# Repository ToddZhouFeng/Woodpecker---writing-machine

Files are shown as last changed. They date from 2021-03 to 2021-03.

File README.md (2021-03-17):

# Woodpecker

> 一个简单、低成本、可DIY的写字机器人
>
> A simple, low price, DIYable writing machine

## 项目介绍

### 为什么我要做这个？

目前大多数写字机器人的成本都很高，淘宝上的最低也要500，而开源的也要2~3百。在我看来，写字只是一件很简单的事，根本不需要这么多钱。因此，我希望能设计出一款低于百元的写字机器人。

我大致看了一下网上的开源方案，比较有代表性的如 github 上的 [peng-zhihui/X-Bot](https://github.com/peng-zhihui/X-Bot) 和 arduino社区的 [写字机器人](https://www.arduino.cn/thread-93897-1-1.html)，使用的基本是 core-XY（XY联动）方案，这种方案的介绍可以看 [peng-zhihui/X-Bot](https://github.com/peng-zhihui/X-Bot)，简单来说就是十字交叉的「同步带+导轨」+两个伺服电机

这种方案基本上可以无缝用于工业了好吧╮(╯-╰)╭，不贵才怪呢！个人使用的无需这么复杂。于是就有了这个项目。下面来说说我的想法。

补充资料：

* [3D打印机设计：关于 CoreXY 与 H-bot 之间的选择](https://blog.libcore.org/?p=291)
* [H-BOT机械手模型](http://bbs.inovance.com/course/67/207)

### 我的想法

作为非机械系学生，我希望结构越简单越好。首先，电机直接控制笔在两个方向上的运动。两者要如何连接呢？自然而然，我想到了线。用线的话，就不能在水平面，而是要在垂直面上控制笔——纸固定在墙上，上面挂两个电机，电机用线吊着笔。显然，这种方案在数学上是可行的，给定两根线长，可以求出笔在纸上的位置。

那么，如何控制笔的起落呢？这个可以借鉴以前的开源方案，用一个小舵机来控制笔的旋转，从而控制笔与纸的接触。

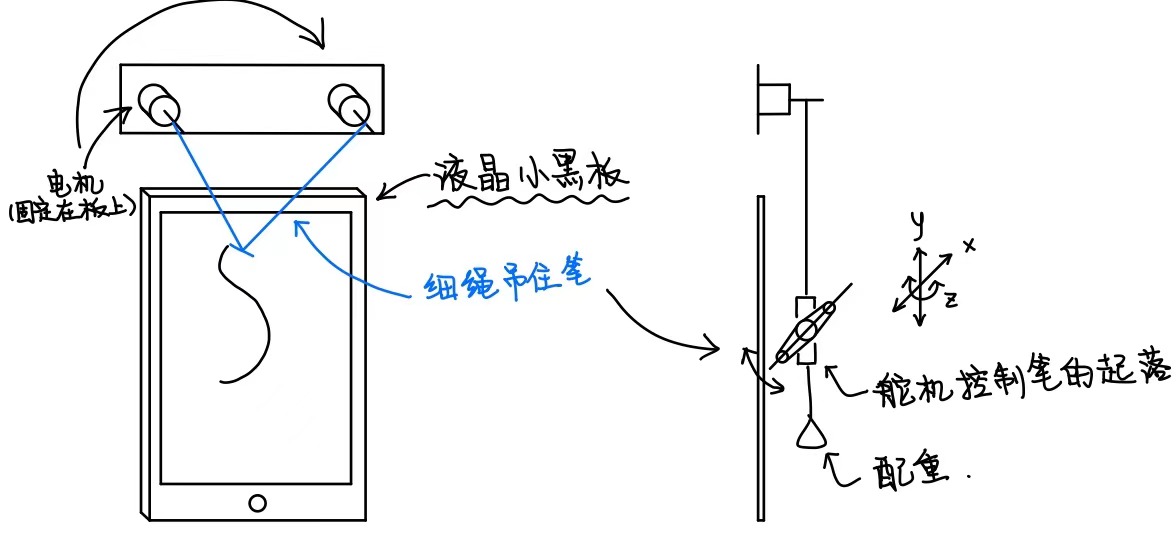
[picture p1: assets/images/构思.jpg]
构思


至此，大概雏形就已经出来了。当然，我不是第一个提出的这种方案的人，网上已经有 DIY 教程：[instructables - Polargraph Drawing Machine](https://www.instructables.com/Polargraph-Drawing-Machine/)，这家伙甚至写好了代码！Bravo！

但这只是节省了导轨的成本，并没有节省伺服电机的成本。于是我想，笔这玩意又没多重，应该用步进电机就行了吧，看网上资料说步进电机没有累积误差，那我直接计算转的圈数就能获取当前的绳长。如果有失步，或许可以通过中途再校正来消除。

OK，想法有了，开干！

## 设计过程

### 硬件

需要的硬件有：

* 步进电机28BYJ-48 + 驱动板 2 套 共￥9.6
* 舵机SG90 1 个 ￥3.9
* 细长线 2 条 ￥0（找妈要）
* 杜邦线母对母、公对母 若干条 ￥1
* 5V电源 1 个 ￥2
* 热熔胶 ￥9.3
* 可选：液晶小黑板（省得老是换纸）米家的贵一点（￥48.9），淘宝上有 ￥9.9 包邮的

总共：￥25.8（不考虑液晶小黑板）

另外还需要控制设备。如果使用上位机与下位机分离的方式，电脑作为上位机，下位机可以是 arduino、stm32、esp8266；如果上位机与下位机一体，可以使用树莓派 zero. 控制设备大概要花费 ￥70

因为我有树莓派，所以我直接在树莓派上控制。

#### 3D 打印

需要 3D 打印的部分有：步进电机固定座、轴套、舵机固定座、笔托。这里问题比较大的是舵机固定座和笔托。因为在初次实验中，我发现写字时笔会歪，导致笔不可能垂直于纸。要解决这个问题，我设想了几个方案：

* 如果是液晶小黑板，则将直杆形的笔换成圆盘性的笔，这样就能解决左右歪的问题，至于上下歪，可以通过增加配重来解决。
* 如果是一般的笔，可以直接在舵机固定座两边加上泡沫支撑
* 双绳方案：增加多一条绳（会增加安装难度

### 软件

第一个问题是，如何将 x-y 坐标的图像，转换为双极坐标？

第二个问题是，给定一条曲线，如何控制步进电机？如果要考虑下笔的轻重，那如何控制舵机？

第三个问题是，如何将图像/文字转化成线？

第四个问题是，怎么规划路径？或者说，怎么决定笔画的顺序？

#### 问题一

双极坐标（Bipolar Coordinates）的定义如下：A,B 是两固定点，距离为 w，平面上任意一对点都可以用到 A,B 的距离 a,b 来表示。详细介绍请去看：[百度百科](https://baike.baidu.com/item/%E5%8F%8C%E6%9E%81%E5%9D%90%E6%A0%87%E7%B3%BB/22803822) 和 [维基百科](https://zh.wikipedia.org/zh-hans/%E9%9B%99%E6%A5%B5%E5%9D%90%E6%A8%99%E7%B3%BB)

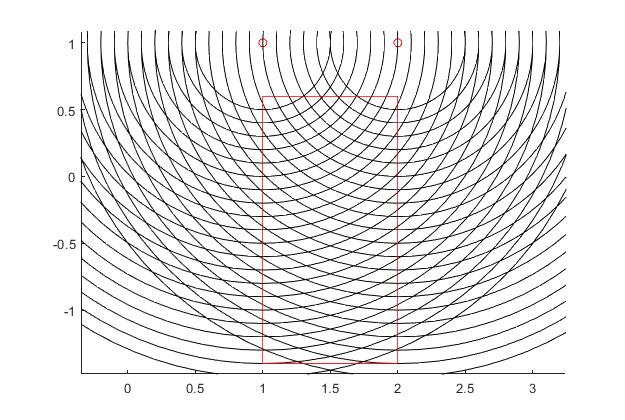
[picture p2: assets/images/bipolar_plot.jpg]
双极坐标


坐标系变换这个应该是在高等数学中学的。我们要实现的就是如下变换：

<center>(x,y)\leftrightarrow(a,b)</center>

一般来说，(x,y) 原点在图像的左下角，但对于悬挂式的写字机器人，图像是从左上角开始画的，所以我们规定左上角是为原点。这么一来，就有：

<center>\begin{cases} a=\sqrt{x^2+y^2}\\ b=\sqrt{(w-x)^2+y^2} \end{cases}</center><br>

<center>\begin{cases} x=\frac{a^2+w^2-b^2}{2w}\\ y=\frac{1}{w}\sqrt{(aw)^2-\left(\frac{w^2+a^2-b^2}{2}\right)^2} \end{cases}</center>

图像转换成双极坐标后，我们就可以像在直角坐标下那样思考。后面默认都是双极坐标。

#### 问题二

步进电机的原理很简单，就是通过磁场的旋转，来带动转子转动。磁场又是通过脉冲控制的，那样只要知道初始位置和脉冲数量，就知道笔的位置。

[步进电机28BYJ-48拆机图、原理和51/stm32测试程序](https://blog.csdn.net/wangguchao/article/details/78902212)

#### 问题三

见 ImagePreprocess

这里我参考了 [Samir55/Image2Lines](https://github.com/Samir55/Image2Lines)、[arthurflor23/text-segmentation](https://github.com/arthurflor23/text-segmentation)、[A Statistical approach to line segmentation in handwritten documents](https://cedar.buffalo.edu/~srihari/papers/SPIE-2007-lineSeg.pdf)

#### 问题四

见 PathDecide

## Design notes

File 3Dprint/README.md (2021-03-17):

# 3D打印模型设计

## 步进电机固定板

28BYJ-48 的尺寸图见：[28BYJ-48 Stepper Motor - RoboCraft](http://robocraft.ru/files/datasheet/28BYJ-48.pdf)

## 步进电机轴套

转轴是一个被削了两刀的圆柱，外圆 4.96mm（取 5mm） 两截面 2.92mm（取 3mm）轴长 6mm，

axis_shell.ptr

## 舵机固定板

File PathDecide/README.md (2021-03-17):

# 路径决策

本模块要解决如何通过位图来驱动电机，这是本项目的核心模块。我们规定以下对象和接口：

* `bitmap` 位图（二维矩阵，值为0或1，1表示要下笔的地方），大小为 a_max × b_map
* `index2length(index_a, index_b)` 由位图像素的索引计算出长度
* `drop()` 和 `lift()`
* `motor_a` 电机a
  * `motor_a.move(thread_length)` 移动到对应长度
* `motor_b` 电机b
  * `motor_b.move(thread_length)` 移动到对应长度

## 扫描法

顾名思义。优点是简单，缺点是慢。

```python
for k in range(a_max):
    for l in range(b_max):
        if bitmap[l,k]==1:
            drop()
        else:
            lift()
        thread_length_a, thread_length_b = index2length(k,l)
        motor_a.move(thread_length_a)
        motor_b.move(thread_length_b)
```

为了提高效率，我们可以考虑采用跳跃扫描法（实际是缩减分辨率）。如下：

```python
for k in range(0,a_max,2):
    for l in range(0,b_max,2):
        if bitmap[l,k]==1 or bitmap[l+1,k]==1 or \
            bitmap[l,k+1]==1 or bitmap[l+1,k+1]==1:
            drop()
        else:
            lift()
        thread_length_a, thread_length_b = index2length(k,l)
        motor_a.move(thread_length_a)
        motor_b.move(thread_length_b)
```

## 深度搜索法

简单来说就是先扫描，当找到第一个下笔点后，从下笔点开始不断向外搜索，并移动。当找不到时，抬笔，再次向外搜索，然后找到下笔点后，再重复前面的过程。如下：

```python
while True:
    index_next=search(image, index_now)
    if index_next == None:
        break
    if not is_next_to(index_next, index_now):
        if is_drop():
            lift()
        else:
            drop()
    thread_length_a, thread_length_b = index2length(index_next[0],index_next[1])
    motor_a.move(thread_length_a)
    motor_b.move(thread_length_b)
    image[index_now[0], index_now[1]] = 0
```

但这只能达到局部最优，而不能达到全局最优。举个例子，假如说要写一个 T 字，显然，先写一横，再写一竖是最快的，但有可能会先写一个“7”，再补回横的后面，这样的效率就不高。

那这样，我想可以先搜索出所有路径（深度优先或广度优先都行），然后从路径中选择一条最短的路径。这种策略就可以解决上面的问题。

但上面的策略并不完美，比如说要写一个 R 字，从左下开始，如果是选择最短的路径，则会写一个“∧”，然后再写上面的圈。但最快的方式显然是先写一竖 |，再写半圈 ﹚，最后写右下一捺，这样可以一笔写完。（不知道说不说得清……）

于是咱的策略又要改变，我们需要知道最短与最长的路径。如果最长的路径可以覆盖当前的连通区域，那么就选择最长的路径，否则，选择最短的路径。

但这种方法的复杂度很高。为了减少复杂度，我认为在搜索路径时，可以只取某几个方向。比如上一步是向上搜索，那么下一步就只能搜索上面的三个像素。（也就是把一段弯折的线看作不同线段）

算了，太复杂了😫别搜索所有路径了，直接按第一段来吧。

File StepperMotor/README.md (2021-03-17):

# 电机驱动

要驱动电机使线到达指定长度，就必须要知道初始长度以及电机步数。初始长度可以通过手动调整到指定位置，或者手动输入初始长度。电机步数则用一个无符号整型记录即可。另外，最好能知道当前转子的状态，这样的话步就能以拍为单位精确调整。

我们用 `steps_now` 来表示电机当前的步数，`step_length` 表示步长（以拍为单位），一拍的转动长度 `stride_length` 约等于 0.0046mm，则线长 `thread_length=steps_now*step_length*stride_length`。

步进电机我们采用 8 拍的驱动方式，即：

| 转子状态 | 0 | 1 | 2 | 3 | 4 | 5 | 6 | 7 |
| --- | --- | --- | --- | --- | --- | --- | --- | --- |
| P1-红 | VCC | VCC | VCC | VCC | VCC | VCC | VCC | VCC |
| P2-橙 | GND | GND | | | | | | GND |
| P3-黄 | | GND | GND | GND | | | | |
| P4-粉 | | | | GND | GND | GND | | |
| P5-蓝 | | | | | GND | GND | GND | |

我们定义当前的转子状态 `motor_state_a` 与步数 `steps_now_a` 、步长 `step_length` 的关系如下：

```python
motor_state = (steps_now_a * step_length) % 8
```

初始化时，用户要调整电机，使得笔恰好对齐某个位置，这个位置的线长是固定的（在组装时设置好），假设是 `init_thread_length`，则初始时的步数为：

```python
steps_now = int(init_thread_length / (step_length * stride_length))
```

但如果我们想要精确到拍的话，上面的初始过程就不够好。所以我们规定，在用户调整电机时，转子始终停在 0 状态，并且初始步数要被 8 整除：

```python
steps_now -= steps_now % 8 
```

之后在写字的过程中，如果要去到 `thread_length` 位置，需要移动的步数为：

```python
int(thread_length/step_length/stride_length)-steps_now
```

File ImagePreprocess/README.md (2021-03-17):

# 图像预处理 ImagePreprocess

对待显示的图像/文字进行预处理，得到适合写字机器人的双极坐标下的二值位图（点阵图）。除了进行坐标变换外，还需要对图像进行一系列处理，以获得更好的显示效果。

处理工序：（名字是我随便起的）

* 像素二值化
* 图像素描化
* 线条归一化
* 上采样/下采样
* 分辨率对齐（坐标变换）

注：工序的顺序有待后续进一步实验。

## 分辨率

对输入的源图像，及输出的位图的分辨率的讨论。

### 液晶板的分辨率

液晶小黑板上的笔记会随写字的力度变化，大概在 0.4~1.5mm 之间。一般的纸和笔则是在0.4~0.7mm 之间。而

* 10英寸米家小黑板的可写面积大概是：150×200mm，也就是说，分辨率最高为 375×500，最低为 100×133
* 淘宝上9.9包邮的8.5英寸小黑板的可写面积为 120×174mm，对应的最高分辨率为 300×435，最低为 80×116

实验时，我们使用8.5英寸的小黑板，并取笔记粗细为 0.6（方便计算），则分辨率为 200×290. 要清晰显示一个汉字，至少要 16×16（不考虑[丁卯点阵体](https://3type.cn/fonts/dinkie_bitmap/index.html)），这么一来，我们一共能显示 12×16=192字，用作备忘录应该可以了（用作情书得增加分辨率才行）。

### 步进电机分辨率

但除了液晶小黑板的分辨率外，我们还要考虑笔的最小移动距离，即步进电机的最小转动距离。

28BYJ-48 是四相八拍减速型步进电机，转子转动一圈需要 64 拍，而减速比为 1:64，从而转轴转一圈需要 4096 拍。（参考自 [太极创客 - 28BYJ-48单极性步进电机](http://www.taichi-maker.com/homepage/reference-index/motor-reference-index/28byj-48-stepper-motor-intro/)）

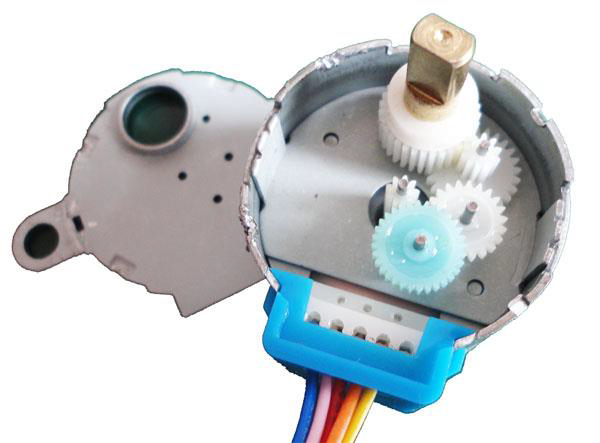
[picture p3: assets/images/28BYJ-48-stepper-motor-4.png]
28BYJ-48步进电机内部拆解图


由于转轴不是圆的，所以需要在外部套上轴套（3D打印），设轴套直径为 5mm，考虑上线缠绕会增加 1mm 左右，也就是总共 6mm。那么，最小转动距离为 π×6÷4096 ≈ 0.0046mm

只有当线垂直时，笔的最小移动距离才等于最小转动距离，当不垂直时，情况会比较复杂，有可能大于也有可能小于最小转动距离（见下图红框的下部，纵向小于，横向大于）

<center>双极坐标下的网格点</center>

由于最小移动距离并不是唯一的，为了避免误解，我们使用“格点距离”来表示笔的移动距离。格点距离 $d$ 可以用如下公式计算：设 P 点的双极坐标为 $(a_p,b_p)$，Q 点的双极坐标为 $(a_q,b_q)$，极点间距为 $w$，则根据余弦公式：

$$
\sec \left( \arccos\left(\frac{a_p^2+w^2-b_p^2}{2a_pw}\right)-\arccos \left( \frac{a_q^2+w^2-b_q^2}{2 a_q w} \right) \right)=\frac{a_p^2+a_q^2-d^2}{2a_p a_q}
$$

我们可以利用反三角函数公式化简：

$$
记\, x=\frac{a_p^2+w^2-b_p^2}{2a_pw}, y=\frac{a_q^2+w^2-b_q^2}{2 a_q w}\\
则\, xy+\sqrt{(1-x^2)(1-y^2)}=\frac{a_p^2+a_q^2-d^2}{2a_p a_q}
$$

继续化简：

$$
\begin{aligned}
    d^2=&a_p^2+a_q^2 - 2 a_pa_q\left(xy+\sqrt{(1-x^2)(1-y^2)}\right)\\
    =&a_p^2+a_q^2 - \frac{(a_p^2+w^2-b_p^2)(a_q^2+w^2-b_q^2)}{2 w^2}\\
    &\frac{1}{2w}\sqrt{(2a_p w)^2 - (a_p^2+w^2-b_p^2)^2 }\sqrt{(2 a_q w)^2 - (a_q^2+w^2-b_q^2)^2}
\end{aligned}
$$

尴尬了，matlab 没装 symbolic math toolbox 求不了导，随便取几组数据吧。取 $w=100$，$\Delta=0.0046$：

|原位置(线长)|移动后|距离|
|-----|-----|---|
|(57.73,57.74)|(+Δ,-Δ)|0.0053|
|(57.73,57.74)|(+Δ,+Δ)|0.0092|
|(186.81,186.82)|(+Δ,-Δ)|0.0172|
|(186.81,186.82)|(+Δ,+Δ)|0.0048|

实际的最小转动距离并不会取这么小，感觉可以乘个 25，故取 $\Delta=0.115$

|原位置(线长)|移动后|距离|
|-----|-----|---|
|(57.73,57.74)|(+Δ,-Δ)|0.1328|
|(57.73,57.74)|(+Δ,+Δ)|0.2293|
|(186.81,186.82)|(+Δ,-Δ)|0.4297|
|(186.81,186.82)|(+Δ,+Δ)|0.1194|

观察上面几组数据，可以得出以下结论：

1. 当笔靠近上面时，横向格点距离与最小转动距离差不多，纵向则是 2 倍关系
2. 当笔靠近下面时，纵向格点距离与最小转动距离差不多，横向则是 4 倍关系
3. 在可写面积内，基本上不会出现格点距离小于最小转动距离的情况，因此可以认为最小格点距离就是最小转动距离。

### 输出位图的分辨率

尽管实际显示的分辨率仅有 200×290（液晶小黑板的分辨率），但输出位图的分辨率应该比这个大。我们可以用下图来说明原因。

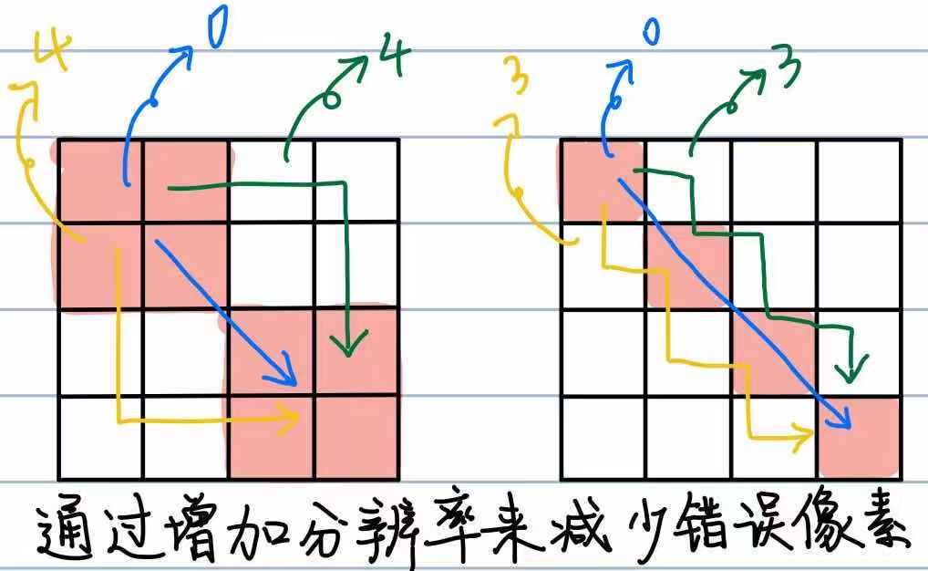
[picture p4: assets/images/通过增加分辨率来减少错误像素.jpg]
通过增加分辨率来减少错误像素


图片中的涂红部分为要落笔的像素点，如果要从一个像素移到另一个像素，可以使用多种驱动电机的方式，最简单的有三种：①先左电机后右电机、②先右电机后左电机、③同时驱动。

同步驱动对控制的要求比较高，并且完全同步是不可能的。而另外两种在移动的过程中都会误涂到空白像素，上图中标出的数字就是误涂面积。一种减少误涂面积的方法就是增加分辨率，减小每次移动的距离。

当然，图像的分辨率也不是越大越好，太大的话，后面路径规划的计算时间会很长，并且画图的时间也很长。另外，分辨率的上限也受到最大格点距离（最小转动距离）的影响。~~如果取最小转动距离为 0.115（25拍）：宽 120/0.115=1043，高 174/0.115=1513（大概是 1080P）~~。

输出位图具体的分辨率将在“分辨率对齐”一节再深入讨论。

## 分辨率对齐（坐标变换）

分辨率对齐指的是数字图像映射到实际的纸上，此处的“数字图像”有两个：输入的源图像以及输出的位图。理想的情况是源图像和位图均重合于实际的纸上，不过实际中必然存在一定偏差，我们要尽可能减小偏差。

首先我们需要确定两电机之间、纸于电机之间的距离。

两电机无论是直接粘在墙上，还是先粘在框架上，它们之间的距离大概能精确至 1mm。假设这个距离是 $w$. 同时，我们假设两电机在一条水平线上（误差 $\pm 1^\circ$），这样，我们就能在空间中建立双极坐标系和直角坐标系（以坐电机为原点）。

我们又假设纸是正的（误差 $\pm 1^\circ$），左上、右上、右下、左下角用 $P_1,P_2,P_3,P_4$ 表示。设纸的左上角 $P_1$ 点的直角坐标为 $(x_1,y_1)$，纸的宽度为 $w_p$，高度为 $h_p$（同样精确到 1mm）。

设源图像的分辨率为 $w_i \times h_i$，并且图像尽可能铺满纸。那么，纸上的每个点 $(x,y) \in \mathbb{R}^2$ 与像素 $(m,n) \in \mathbb{N}^2$ 满足如下对应关系：

$$
w_g = \min\{ \frac{w_p}{w_i}, \frac{h_p}{h_i} \}\\
\lceil\frac{x-x_1}{w_g}\rceil=m\\
\lceil\frac{y-y_1}{w_g}\rceil=n \tag{1}
$$

这里的像素从左上角开始数起，恰好与 opencv 中一致。$w_g$ 是像素格（grid）的边长。上述就是输入的源图像映射到纸上的过程

然后我们再将位图映射到纸上。不过我们需要先确定位图的分辨率。假设最小转动距离为 $w_r$，线的长度的取值范围为：

$$
a\in[\sqrt{x_1^2+y_1^2},\sqrt{x_3^2+y_3^2}]\\
b\in[\sqrt{(w-x_2)^2+y_2^2},\sqrt{(w-x_4)^2+y_4^2}] \tag{2}
$$

则分辨率为：$\lceil\dfrac{a_\max}{w_r}\rceil\times\lceil\dfrac{b_\max}{w_r}\rceil$，其中每个像素点 $(k,l) \in \mathbb{N}^2$ 与空间中的点 $(x,y) \in \mathbb{R}^2$ 满足如下对应关系：

$$
\frac{(k w_r)^2+w^2-(lw_r)^2}{2w}=x\\ 
\frac{1}{w}\sqrt{(k w_rw)^2-\left(\frac{w^2+(k w_r)^2-(lw_r)^2}{2}\right)^2}=y \tag{3}
$$

把公式 $(3)$ 代入公式 $(1)$ 就能得到不同坐标下的像素对应关系：

$$
m=\lceil\frac{(k w_r)^2+w^2-(lw_r)^2}{2ww_g}-\frac{x_1}{w_g}\rceil\\
n=\lceil \frac{1}{w w_g}\sqrt{(k w_rw)^2-\left(\frac{w^2+(k w_r)^2-(lw_r)^2}{2}\right)^2}-\frac{y_1}{w_g}\rceil
$$

python 程序见 cartesian2bipolar_v1.py，输入 (2000, 1500, 3) 的图片，最小转动距离取 0.0046mm，输出 (2333, 2333, 3) 的图片。经过处理后的图像为（左：输入；右：输出）：

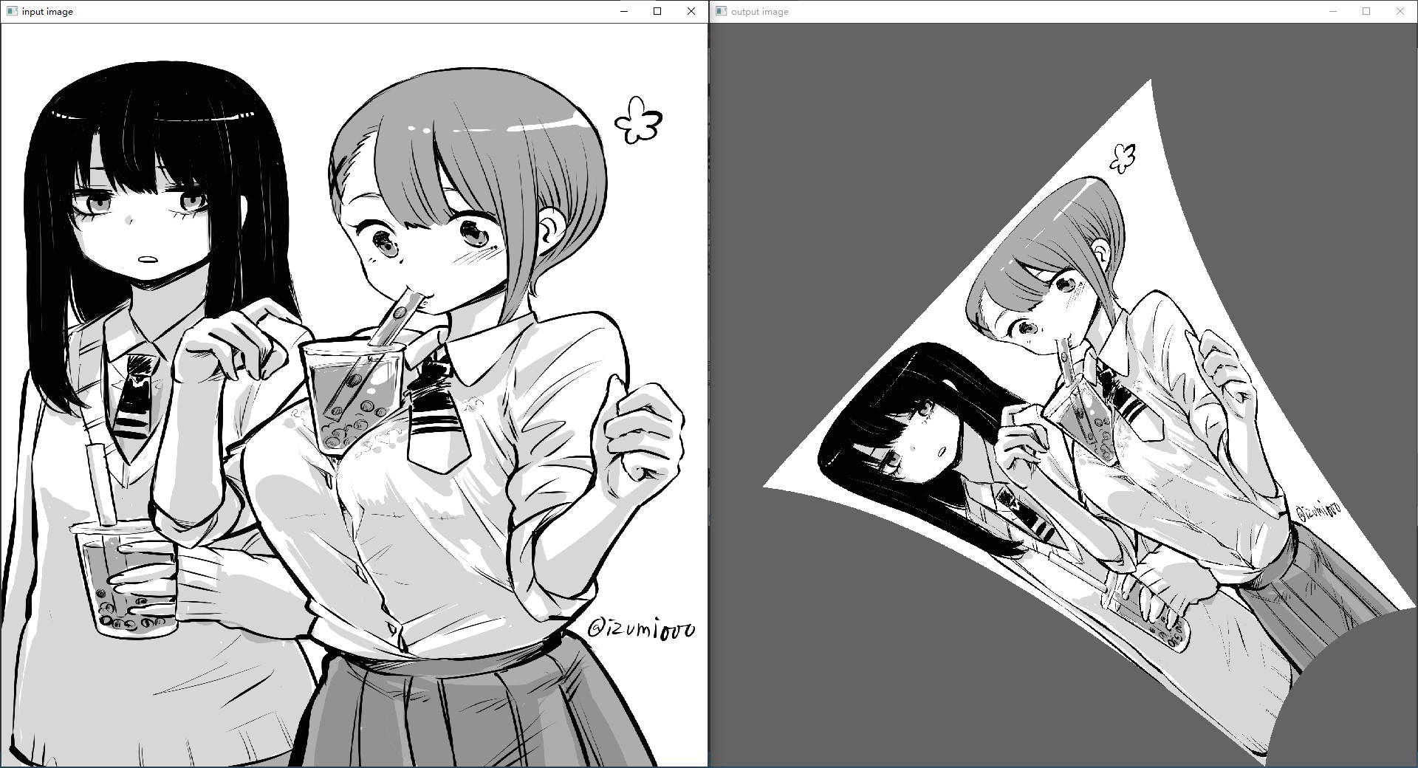
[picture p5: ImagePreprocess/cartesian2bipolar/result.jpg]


为了对比明显，我将图像外部用灰色来填充（实际中应该为纯白色）。注意到位图右下角好像被“挤压”了，说明这部分的图像清晰度有损失。（这也是这种写字机器人的缺点，图像的清晰度不均匀）

为了减小这部分损失，减小清晰度不均匀，我提出以下几种方案：

### 纸下移方案

尝试修改纸与电机的距离，从上面的 10mm，改为 100mm，得到下图：

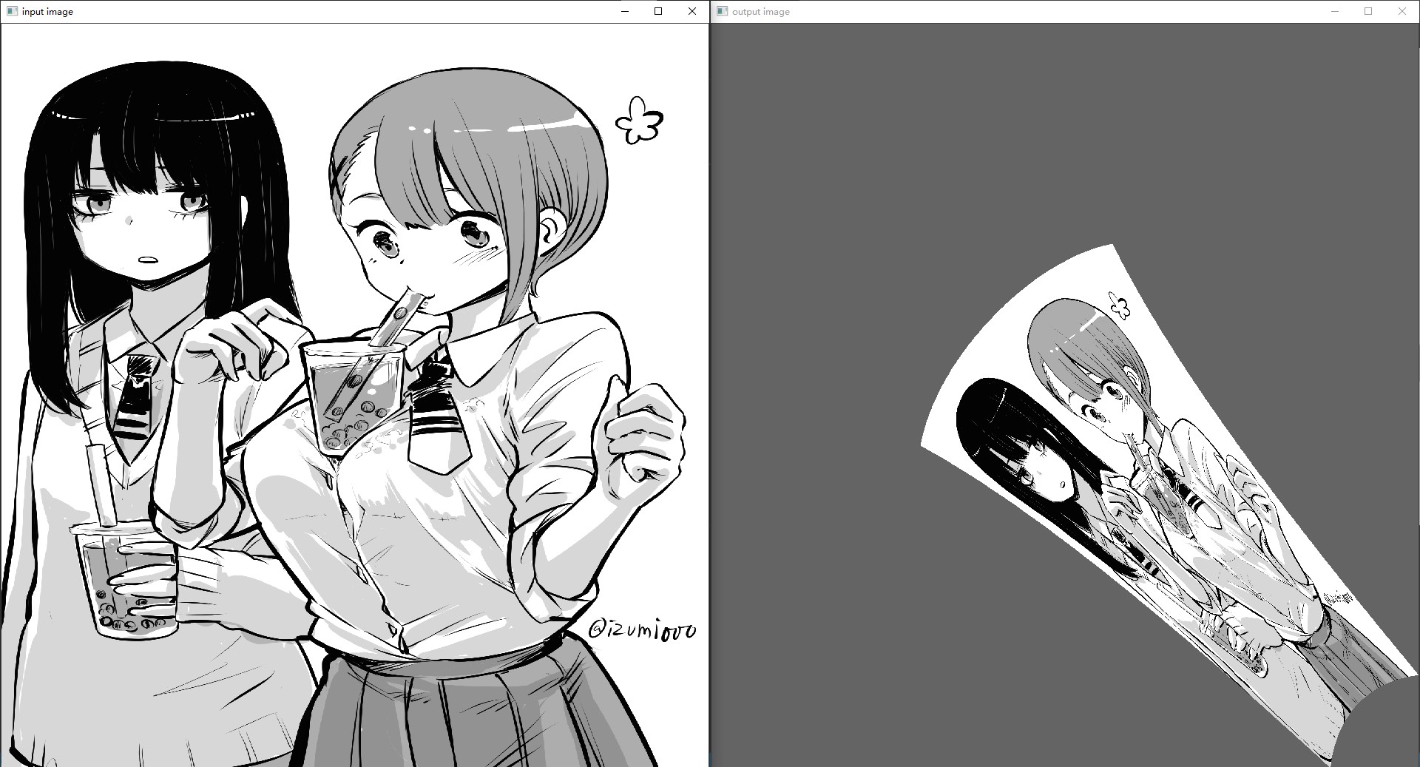
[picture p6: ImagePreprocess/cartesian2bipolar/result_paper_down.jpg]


注意到顶部和底部的分辨率差距减小了。这种方案的优点是：简单无脑。缺点嘛，就是使得写字机器人的占地变大了。

### 动态转动距离方案

引入“动态转动距离”方案。根据在“步进电机分辨率”一节的实验结论，当 $y$ 较小时（顶部），横向格点距离较大，当 $y$ 较大时（底部），横向格点距离较小。因此我们只需要改变一下位图像素索引与绳长的映射关系。原本的映射关系为：$(k,l)\rightarrow (kw_r,lw_r)$，现在假设映射关系为：$(k,l)\rightarrow (kw_r(y),lw_r(y))$，需要求解函数：$w_r(y)$

这个函数还挺复杂的……为了简单起见，我们规定转动距离取 $[w_{r\min},w_{r\max}]$ 中的整数值，即：

$$
w_r(y_\min)= w_{r\max}\\
w_r(y_\max)= w_{r\min}
$$

同时，观察位图左下的灰白交界线，感觉 $w_r(y)$ 应该是一个 $\ln$ 或 $\sqrt{\quad}$ 函数，假如是 $\ln$ 的话：

$$
w_r(y)= \lceil w_{r\min}+\frac{w_{r\max}-w_{r\min}}{\ln (y_\max-y_\min+1)}\ln (y_\max-y+1) \rceil
$$

假如是 $\sqrt{\quad}$ 的话：

$$
w_r(y)= \lceil w_{r\min}+\frac{w_{r\max}-w_{r\min}}{\sqrt{y_\max-y_\min}}\sqrt {y_\max-y}\rceil
$$

但是要求解 $y$，就必须要知道绳长……因此这种方案被我pass了

### 椭圆坐标方案

> 这个方案有点炫技的意味。

观察格点，我发现底部的曲率较大，这可能是造成底部格点距离较大的原因。因此我想能不能利用椭圆两端曲率较大的特点，减小底部的格点距离。

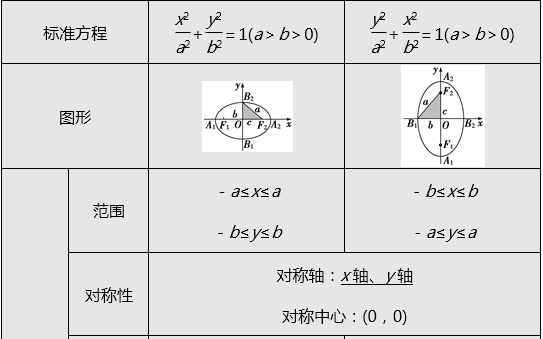
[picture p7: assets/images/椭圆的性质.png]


为此，我们需要对双极坐标进行改造。原本双极坐标的两个坐标变量 $(a,b)=(kw_r,lw_r)$ 表示的是到两个极点的距离，现在要变成椭圆坐标，每个极点需要改成两个焦点，同时，$(a,b)$ 表示为一对焦点间的距离。如果我们定义两个椭圆的表达式为：

$$
\frac{y^2}{a_A^2}+\frac{x^2}{b_A^2}=1\\
\frac{y^2}{a_B^2}+\frac{(x-w)^2}{b_B^2}=1\\
A 指左边的椭圆，B 指右边的椭圆
$$

$a_A,a_B$ 与 $b_A,b_B$ 保持某个比例，定义为 $\frac{a_A}{b_A}=\frac{a_B}{b_B}=\sec \beta$. 另外，$a_A=a$，$a_B=b$，即长轴的一半，这样的话，当 $\sec \beta=1$ 时，这种方案就能退化为之前的方案。

如果 $\sqrt{a_A^2-b_A^2} + \sqrt{a_B^2-b_B^2} \geq w$，则两个椭圆存在交点，交点求解如下：

$$
y^2+\frac{a_A^2 x^2}{b_A^2}=a_A^2\\
y^2+\frac{a_B^2(x-w)^2}{b_B^2}=a_B^2
$$

两式相减，有：

$$
[x^2-(x-w)^2]\cdot \sec^2 \beta = a_A^2-a_B^2
$$

整理后有：

$$
x=\frac{a_A^2-a_B^2}{2w\sec^2 \beta}+\frac{w}{2}
$$

代入回原式有：

$$
y=\sqrt{a_A^2-x^2 \sec^2 \beta}\\
（只取正值）
$$

实际的绳长为：

$$
\begin{cases} 
a'=\sqrt{x^2+y^2}\\ 
b'=\sqrt{(w-x)^2+y^2} 
\end{cases}
$$

另外我们还要计算位图的分辨率。纸的四个角还是用 $P_1,P_2,P_3,P_4$（左上、右上、右下、左下）表示，对应坐标为 $(x_1,y_1)$……，则 $a,b$ 的取值范围为：

$$
a\in \left[\sec \beta \sqrt{\frac{y_1^2}{\sec^2 \beta}+x_1^2}, \sec \beta \sqrt{\frac{y_1^3}{\sec^2 \beta}+x_1^3} \right]\\
b\in \left[\sec \beta \sqrt{\frac{y_2^2}{\sec^2 \beta}+x_2^2}, \sec \beta \sqrt{\frac{y_4^3}{\sec^2 \beta}+x_4^3} \right]
$$

下面是这种方案的验证结果，$\sec \beta$ 取 $1.2$（程序见 cartesian2bipolar_v2.py）

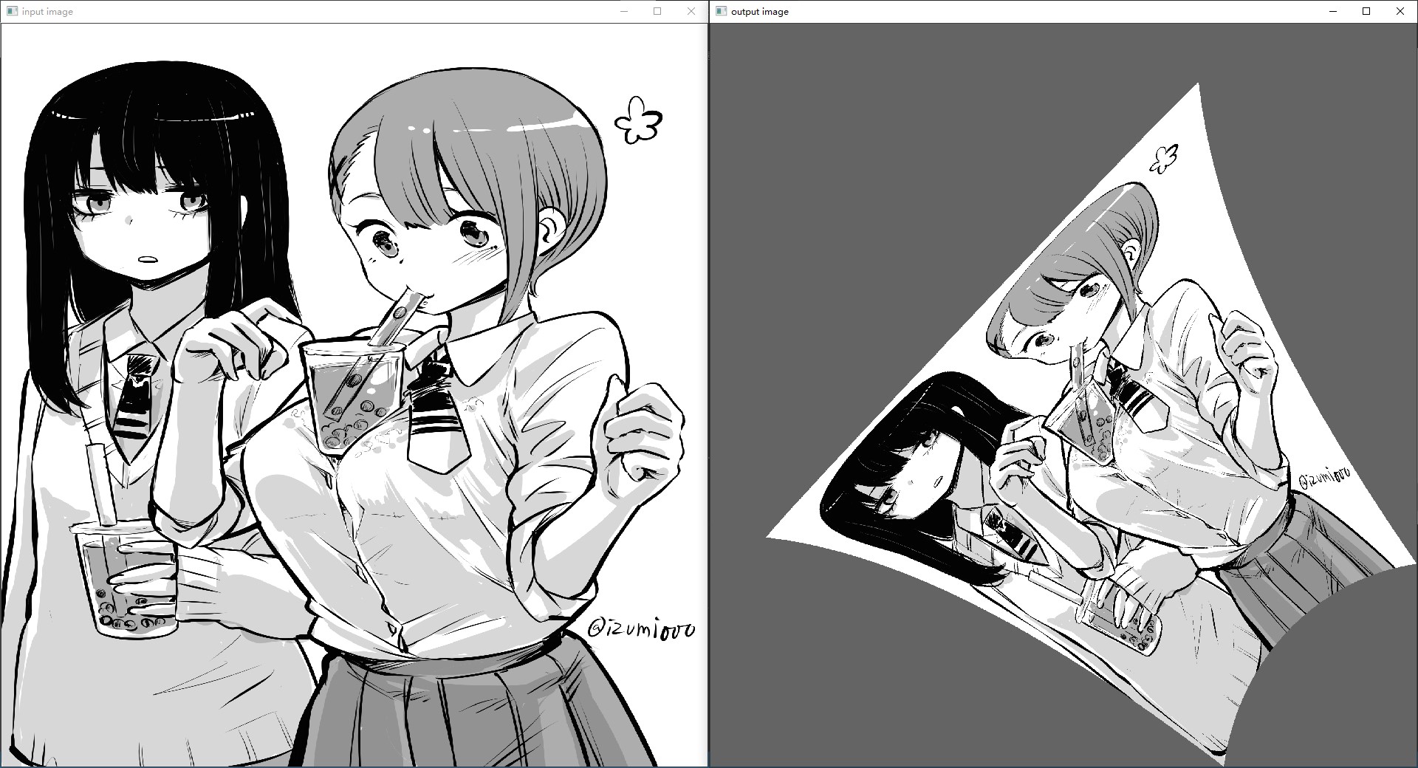
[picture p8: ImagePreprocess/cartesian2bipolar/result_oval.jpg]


|方案|结果|分辨率|有效像素点（图像区域）|
|---|----|----|----|
|无改进方案||2333x2333|1 919 475|
|纸下移方案||2985x2985|1 705 659|
|椭圆坐标方案||2524x2524|2 337 640|

我把几种方案放在一张表格中以方便对比。评价标准如下：

1. 左上角和右下角两条分界线是否等长，长度约接近则效果越好
2. 转换后的图像的比例与原图像越接近越好
3. 有效像素越多说明越精细

从评价标准 1 来看，椭圆>纸下移>无改进。我们原图像的长宽比为 4:3，从评价标准 2 来看，椭圆>纸下移>无改进。从评价标准 3 来看，椭圆>无改进>纸下移。综合来看，椭圆完胜。

当然，从计算角度来说，椭圆坐标最复杂，不过一般都是在电脑上做，处理时间应该差不多。

## 上采样/下采样

现在看来，在坐标变换的过程中已经完成了上采样与下采样。当然，我们依然可以利用深度学习来补充细节，比如 [Bigjpg - AI人工智能图片放大](https://bigjpg.com/) 和 [waifu2x](http://waifu2x.udp.jp/index.zh-CN.html)，这不是本项目的关注点，故不细说。

## 图像素描化

我还没学图像处理，就随便从网上找了一些程序，经过实验后，比较好的是这个：[Python3 用PIL处理图像（二）——将图片装换成素描](https://my.oschina.net/u/4303818/blog/4254663)，代码在 PIL_sketch.py 经过处理的图像如下：

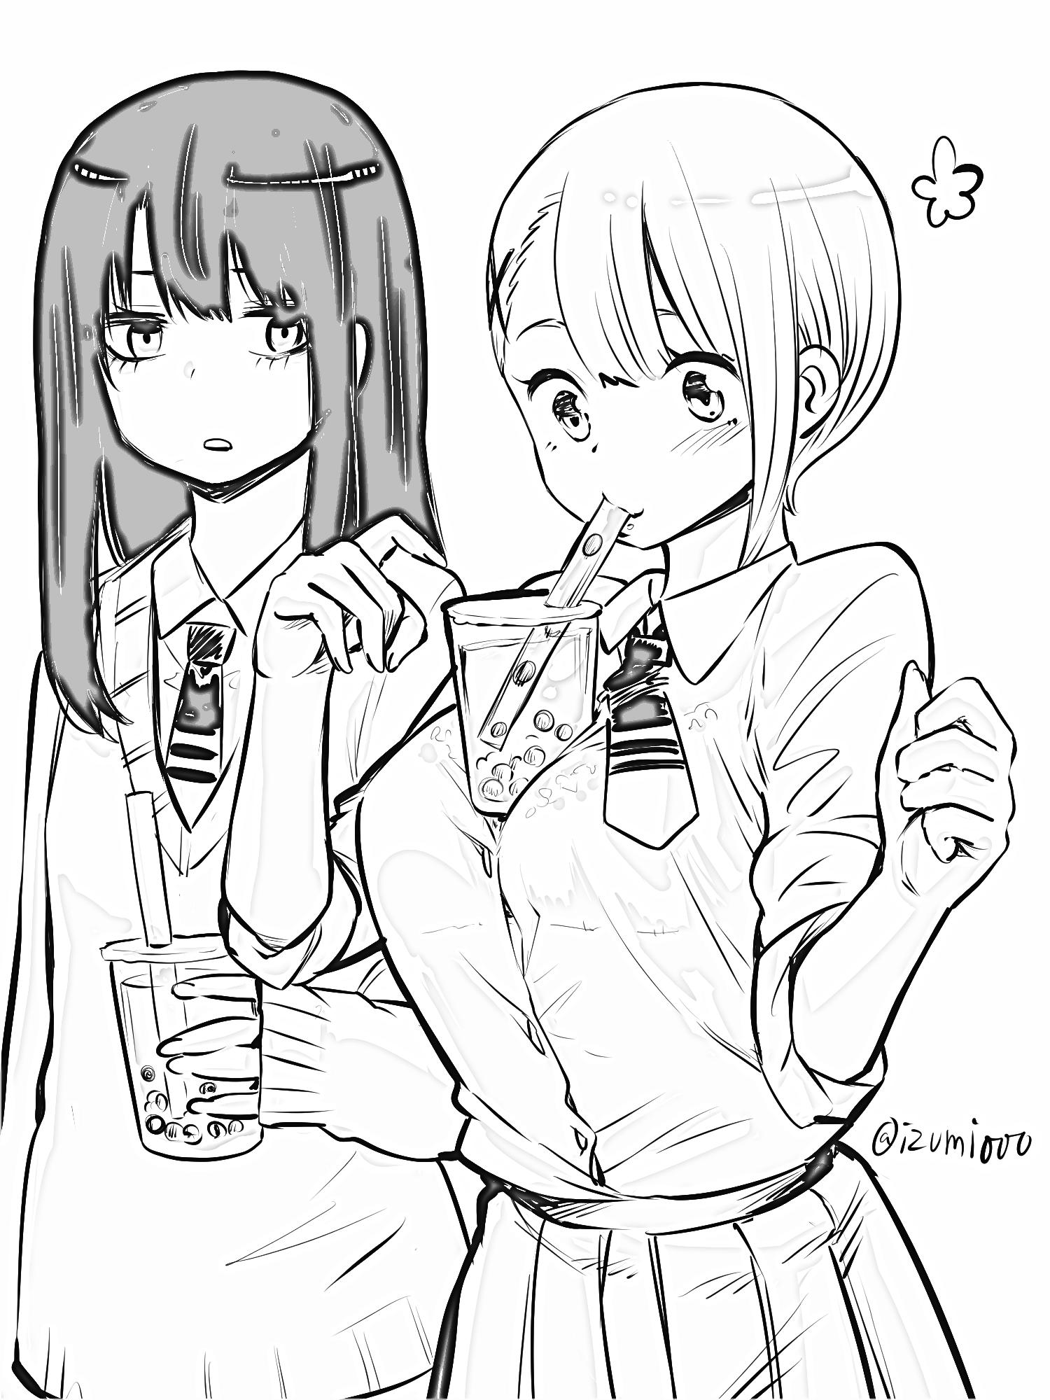
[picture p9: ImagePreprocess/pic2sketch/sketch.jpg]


如果是彩色图片，效果是这样的：

|原图|素描化|
|--|---|
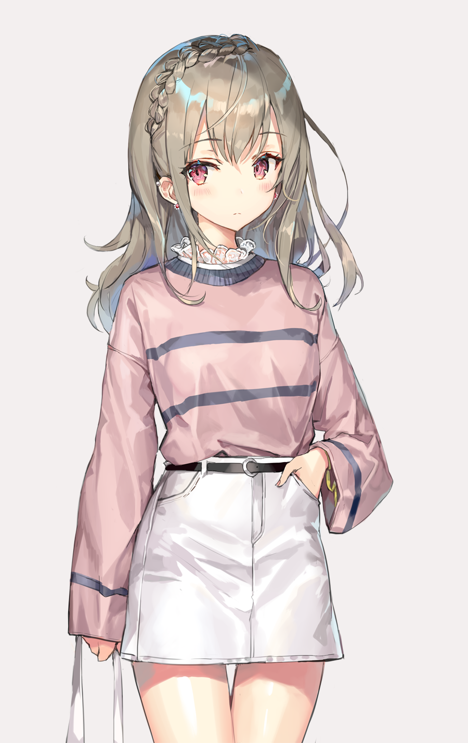
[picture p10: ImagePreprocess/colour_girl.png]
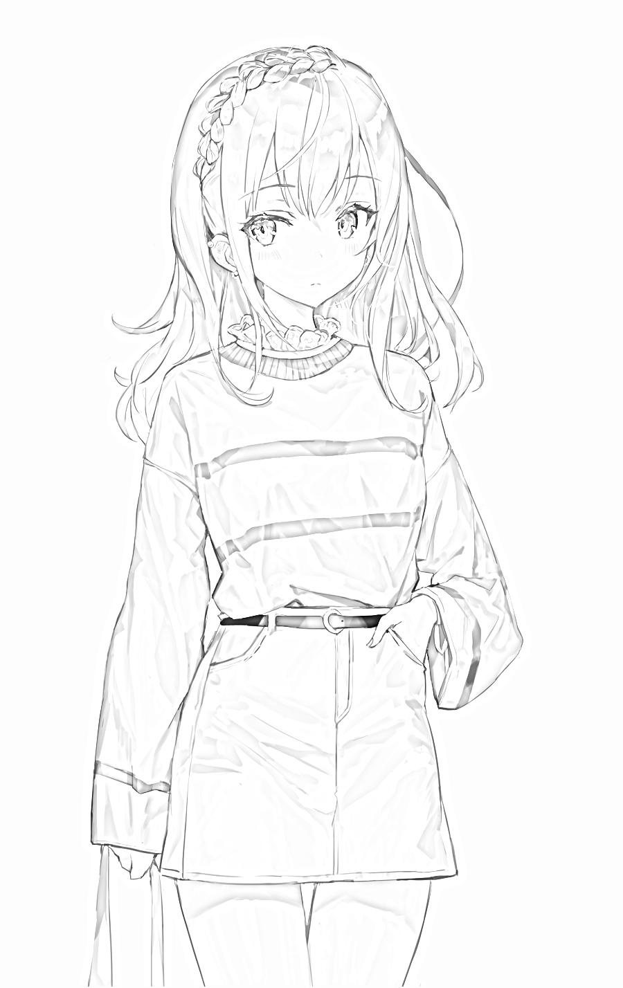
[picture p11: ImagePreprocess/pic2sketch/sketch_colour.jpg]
|||

## 图像二值化

用 [CodecWang - Opencv-Python Tutorial](http://codec.wang/#/opencv/start/06-image-thresholding) 上的代码对原图像（未经素描化）进行处理，代码在 adaptive.py 和 otsu.py，得到下面几种结果：

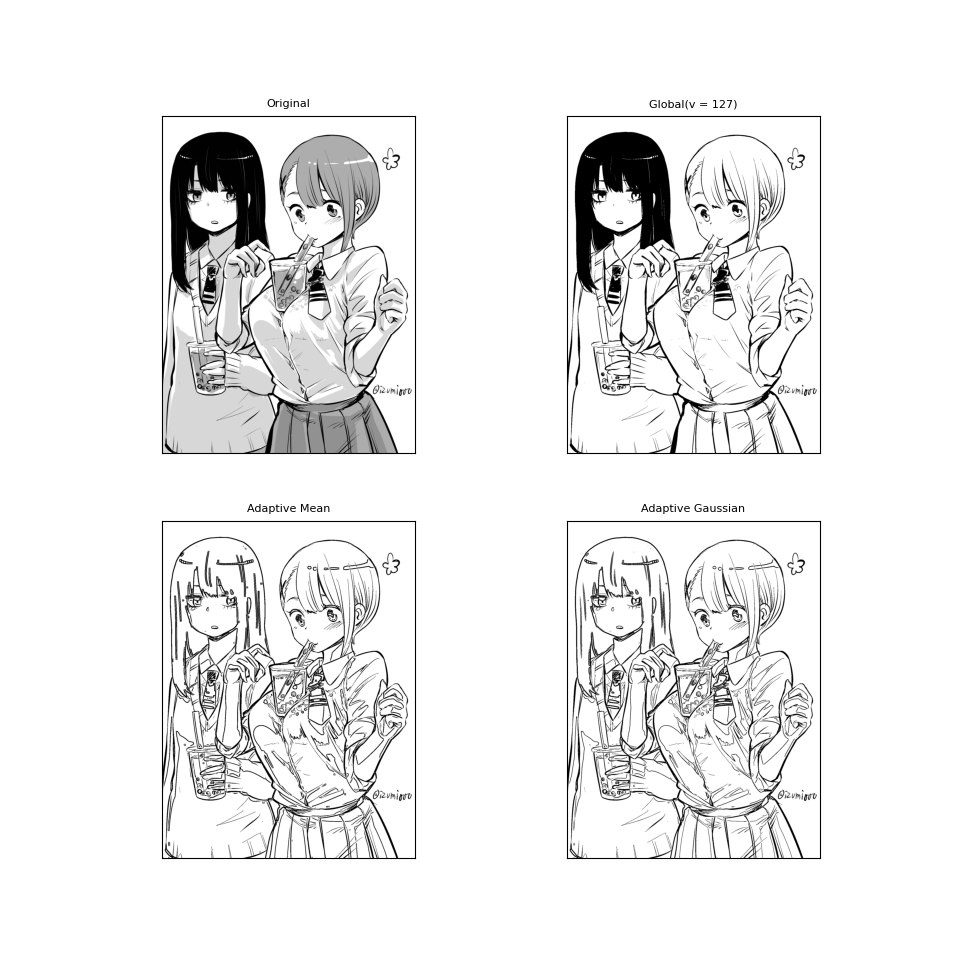
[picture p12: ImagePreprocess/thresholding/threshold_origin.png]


对素描化的图像进行处理，得到下面几种结果：

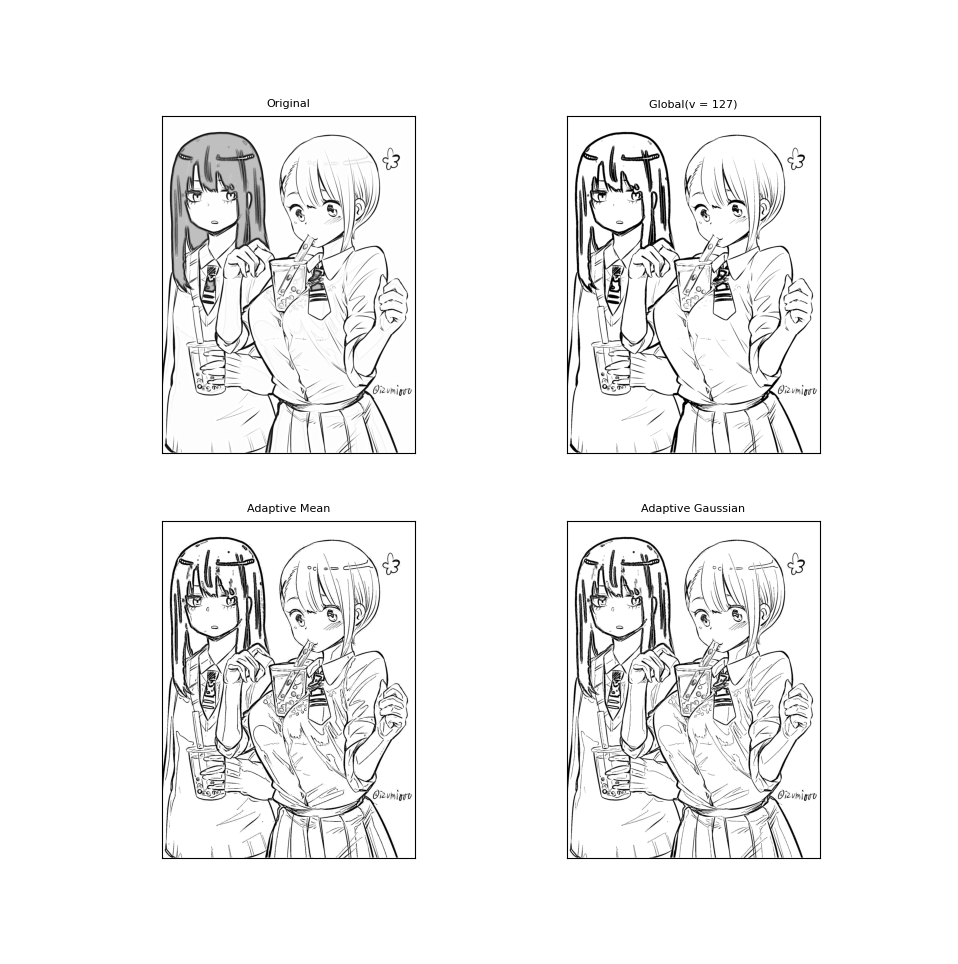
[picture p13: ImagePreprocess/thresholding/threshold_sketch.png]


另外，还有使用 Otsu 方法：

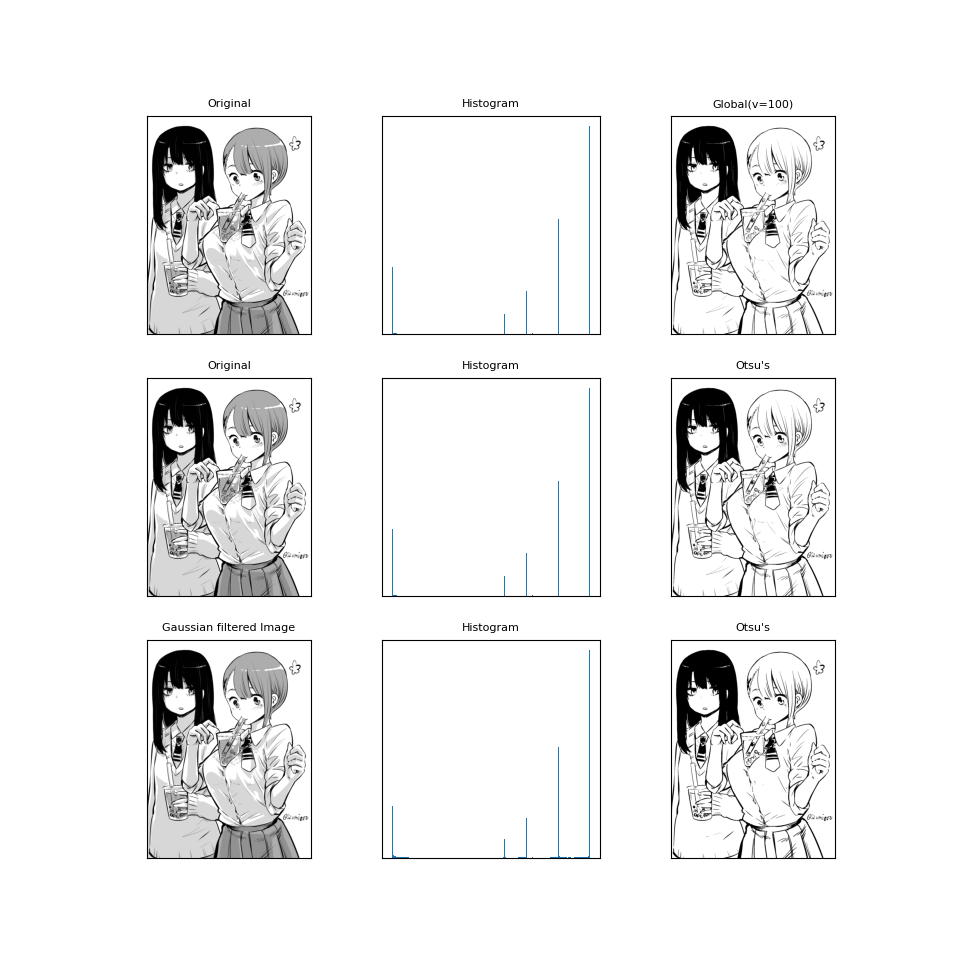
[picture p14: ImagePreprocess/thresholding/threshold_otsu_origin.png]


好像……都差不多？主要区别就是头发和衣服，另外，经过素描化再二值化反而效果不好。算了，不管这么多了，反正都作为选项，由用户自行选择。

## 图像线条正则化（归一化）

参考了：[线稿处理LineCloser及LineNormalizer](https://zhuanlan.zhihu.com/p/44447467)

线条正则化就是统一粗细，这样就不用反复涂了。另外，在正则化前，还需要进行线条闭合化，将线的缺口补回去。这需要利用深度学习来完成，我是在 colab 上弄的。

我选取了 gaussian+otsu 处理后的图片，经过 LineCloser处理后，有：

|原图|对比|LineCloser处理后|
|---|---|---|
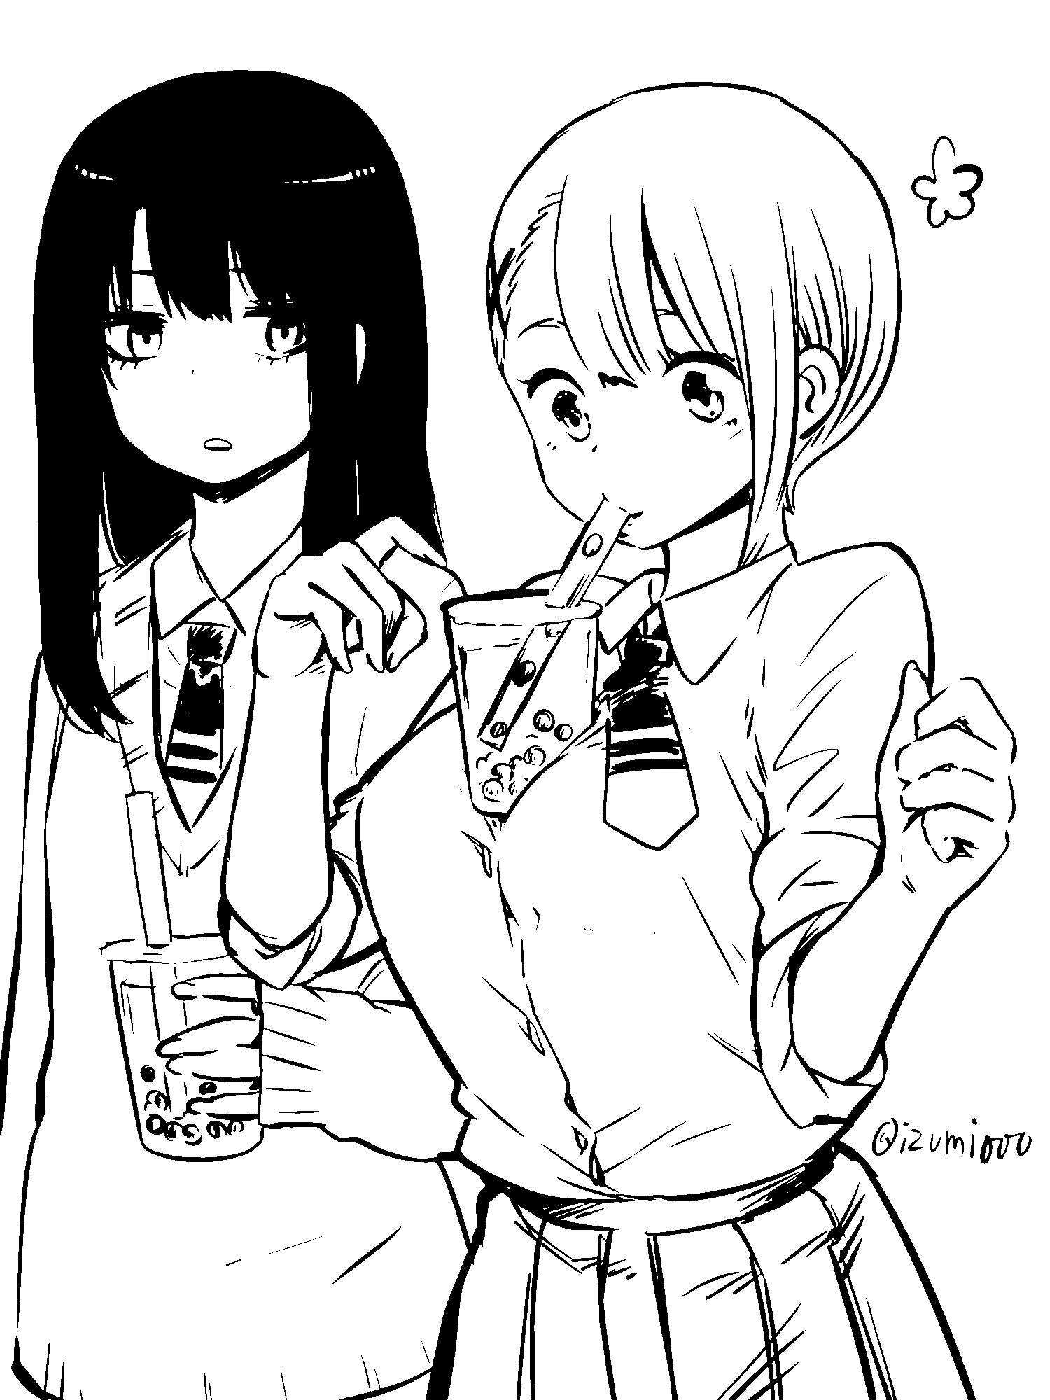
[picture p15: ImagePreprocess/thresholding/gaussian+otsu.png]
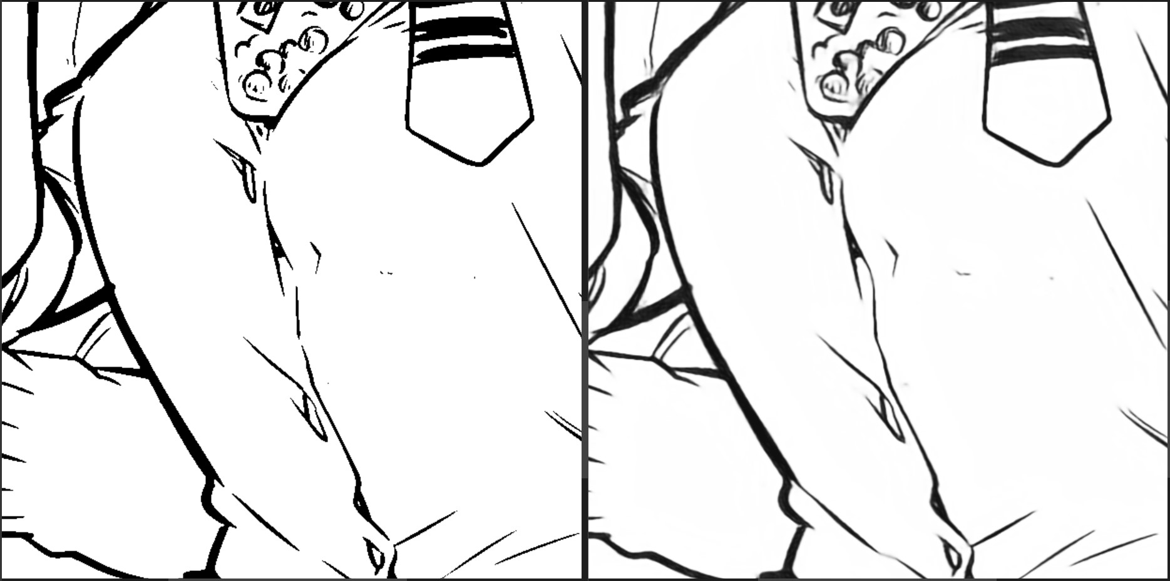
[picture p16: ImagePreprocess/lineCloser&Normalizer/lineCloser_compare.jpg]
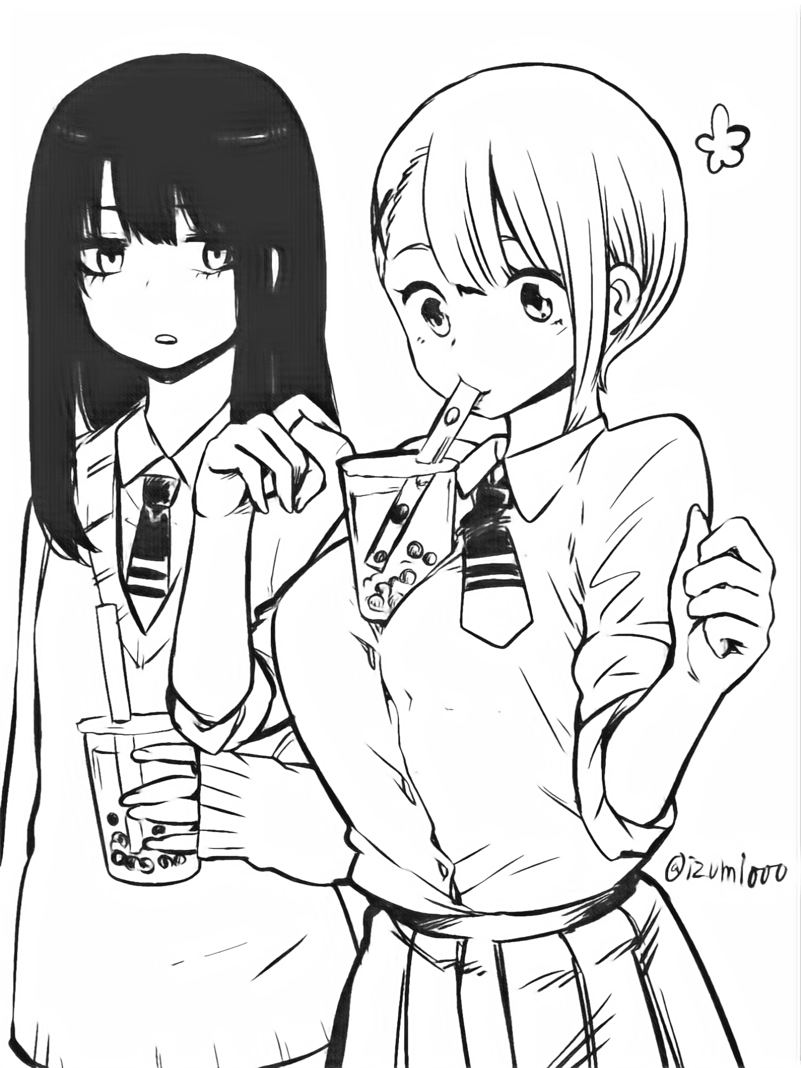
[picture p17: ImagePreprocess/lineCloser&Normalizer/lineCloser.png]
||||

然后进一步用 LineNormalizer 处理，处理完后图像部分变成灰色，需要重新用otsu处理

|LineCloser处理后|对比|LineCloser+LineNormalizer+otsu处理后|
|---|-----|---|
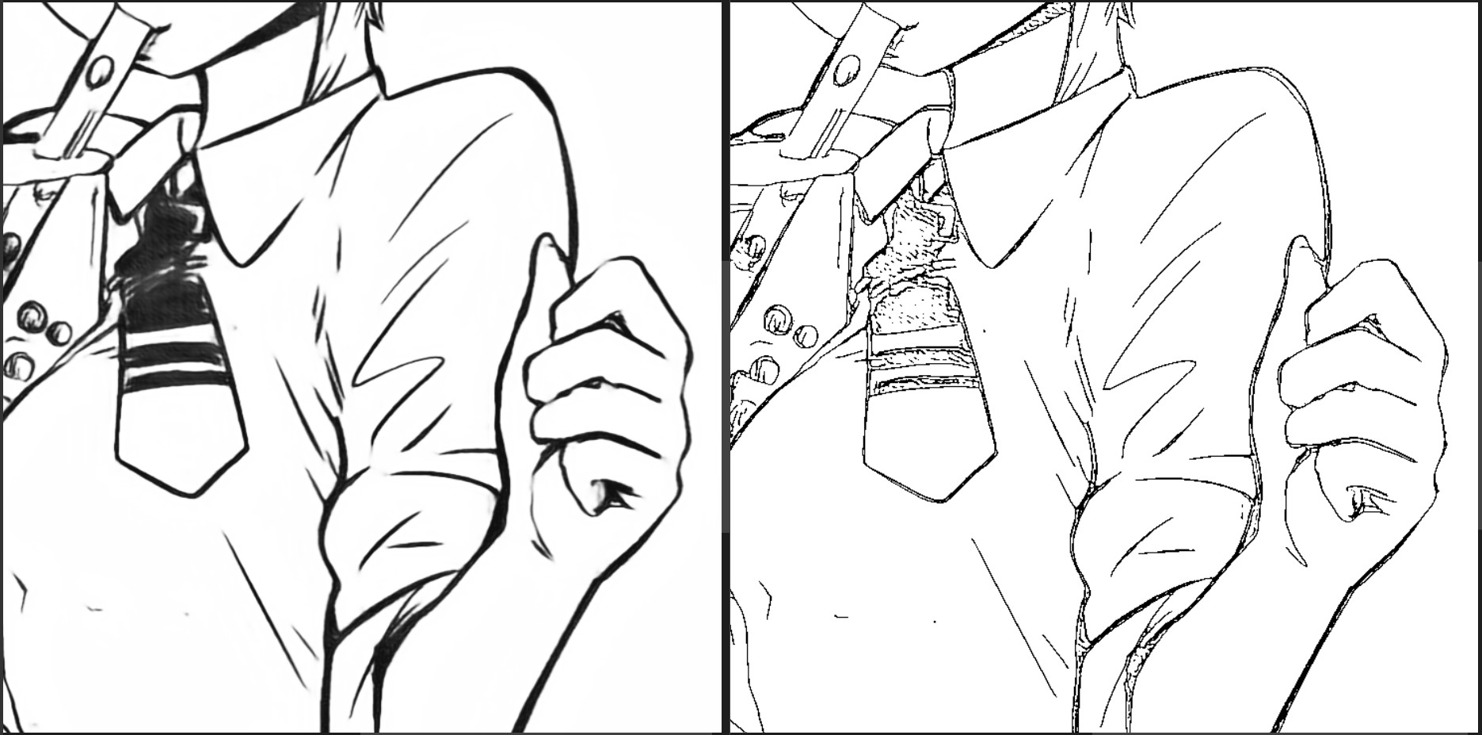
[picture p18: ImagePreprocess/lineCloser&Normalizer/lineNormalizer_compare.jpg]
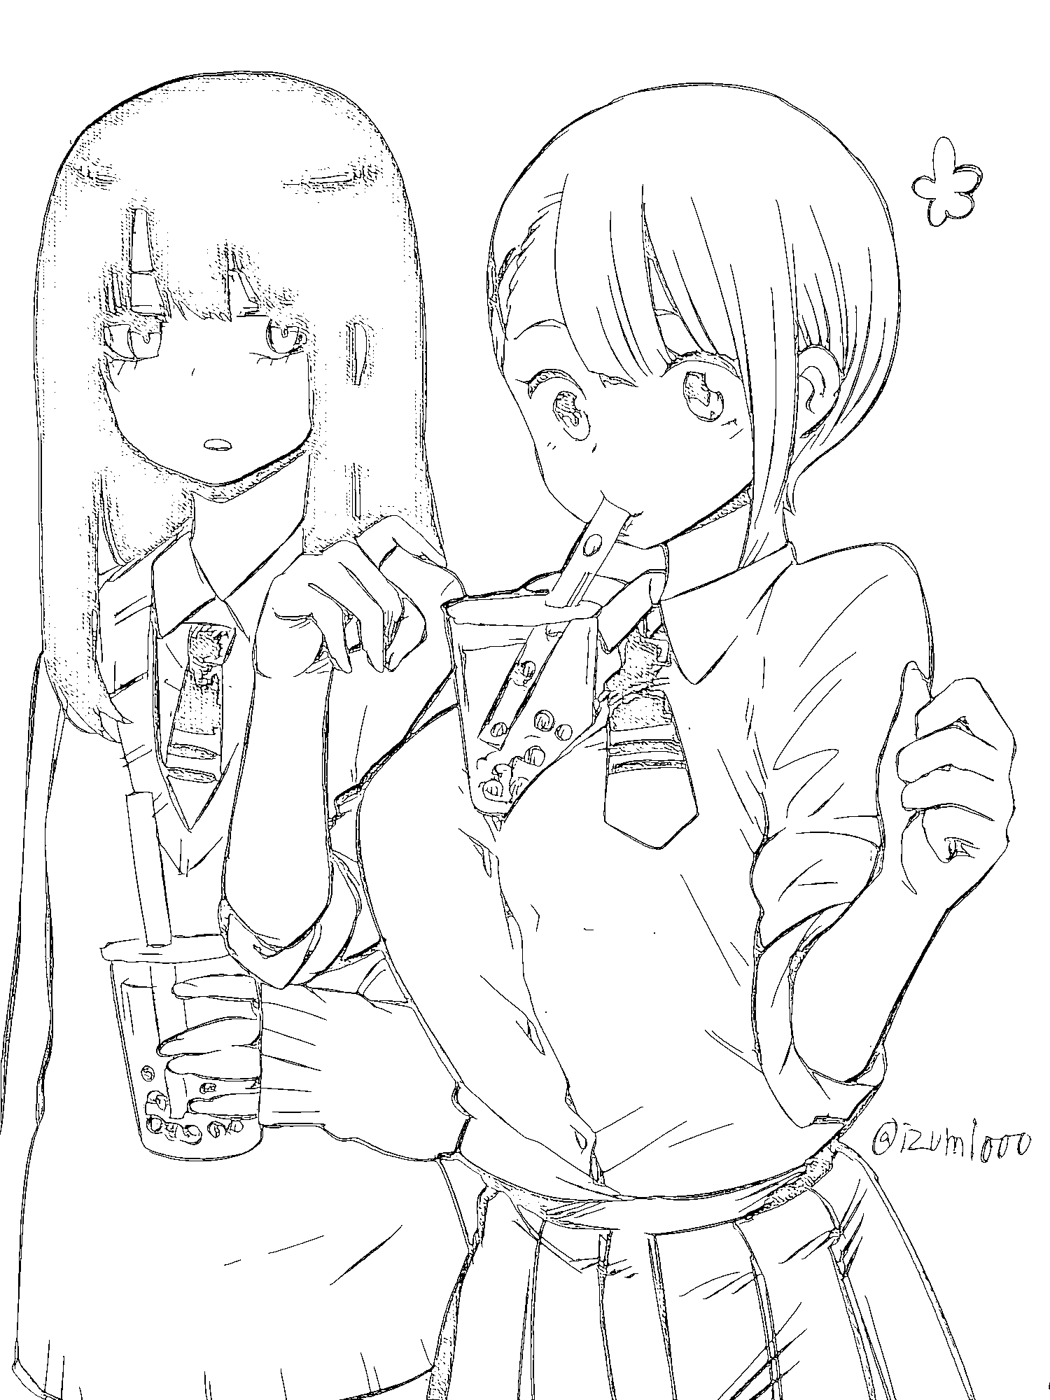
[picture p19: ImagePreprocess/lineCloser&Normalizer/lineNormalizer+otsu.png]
||||

经过一系列处理后，将粗线用一条或两条细线代替，可以提高写字机器人的效率。但是要注意的是，LineNormalizer 最好在坐标变换后再做，因为坐标变换会导致某些线变得破碎（见下面对照）

|lineNormalizer+c2o|c2o+lineNormalizer|
|---|---|
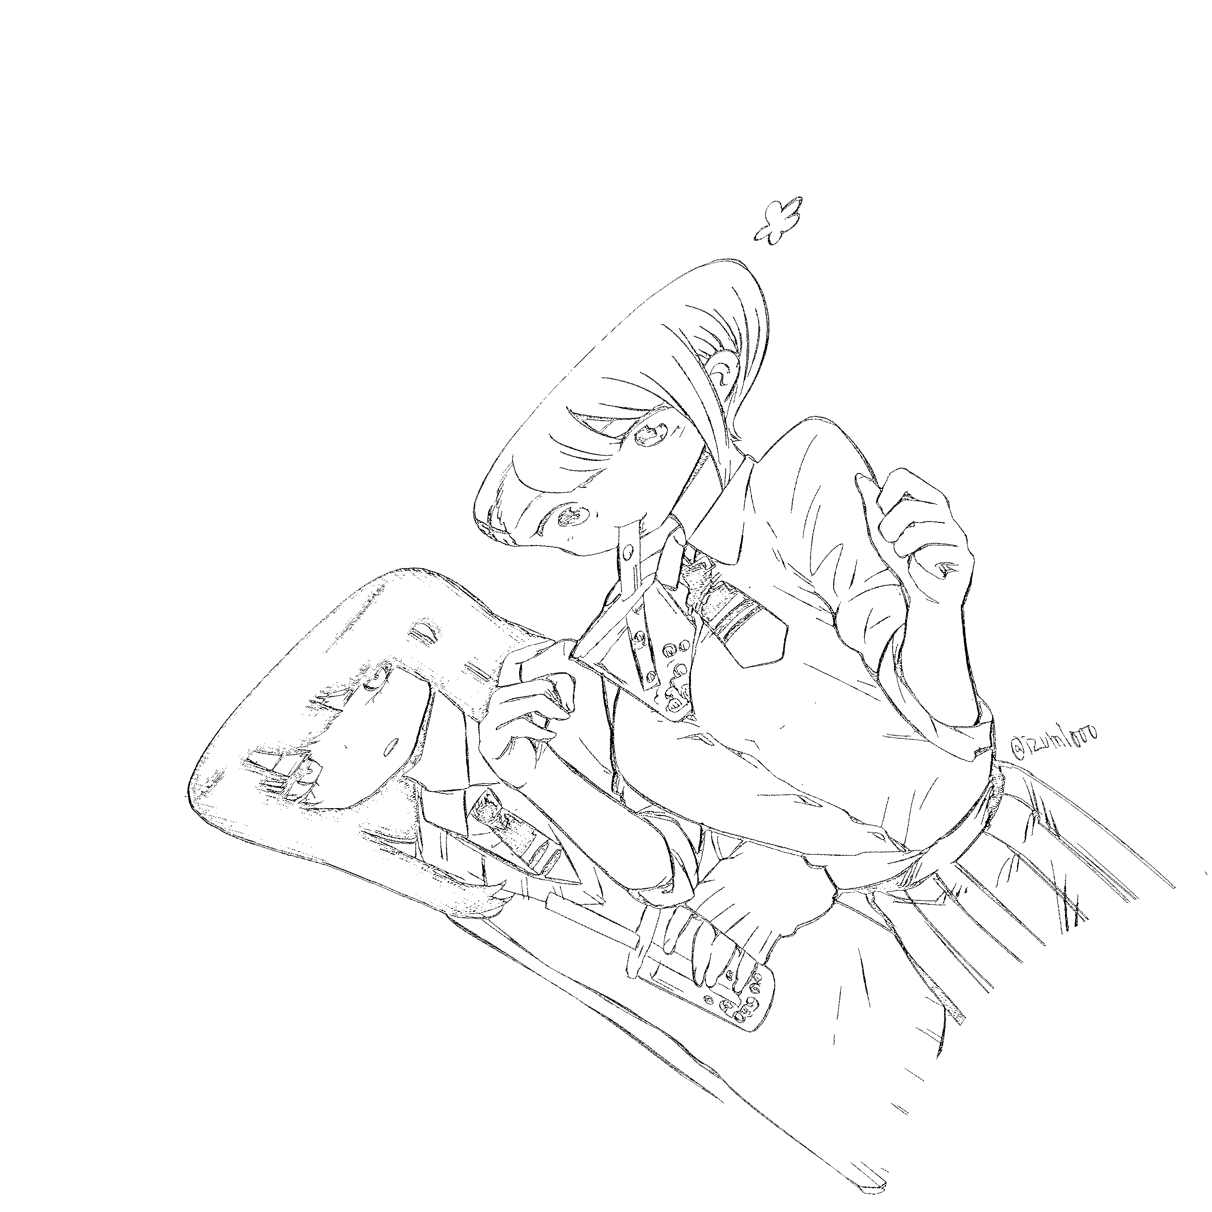
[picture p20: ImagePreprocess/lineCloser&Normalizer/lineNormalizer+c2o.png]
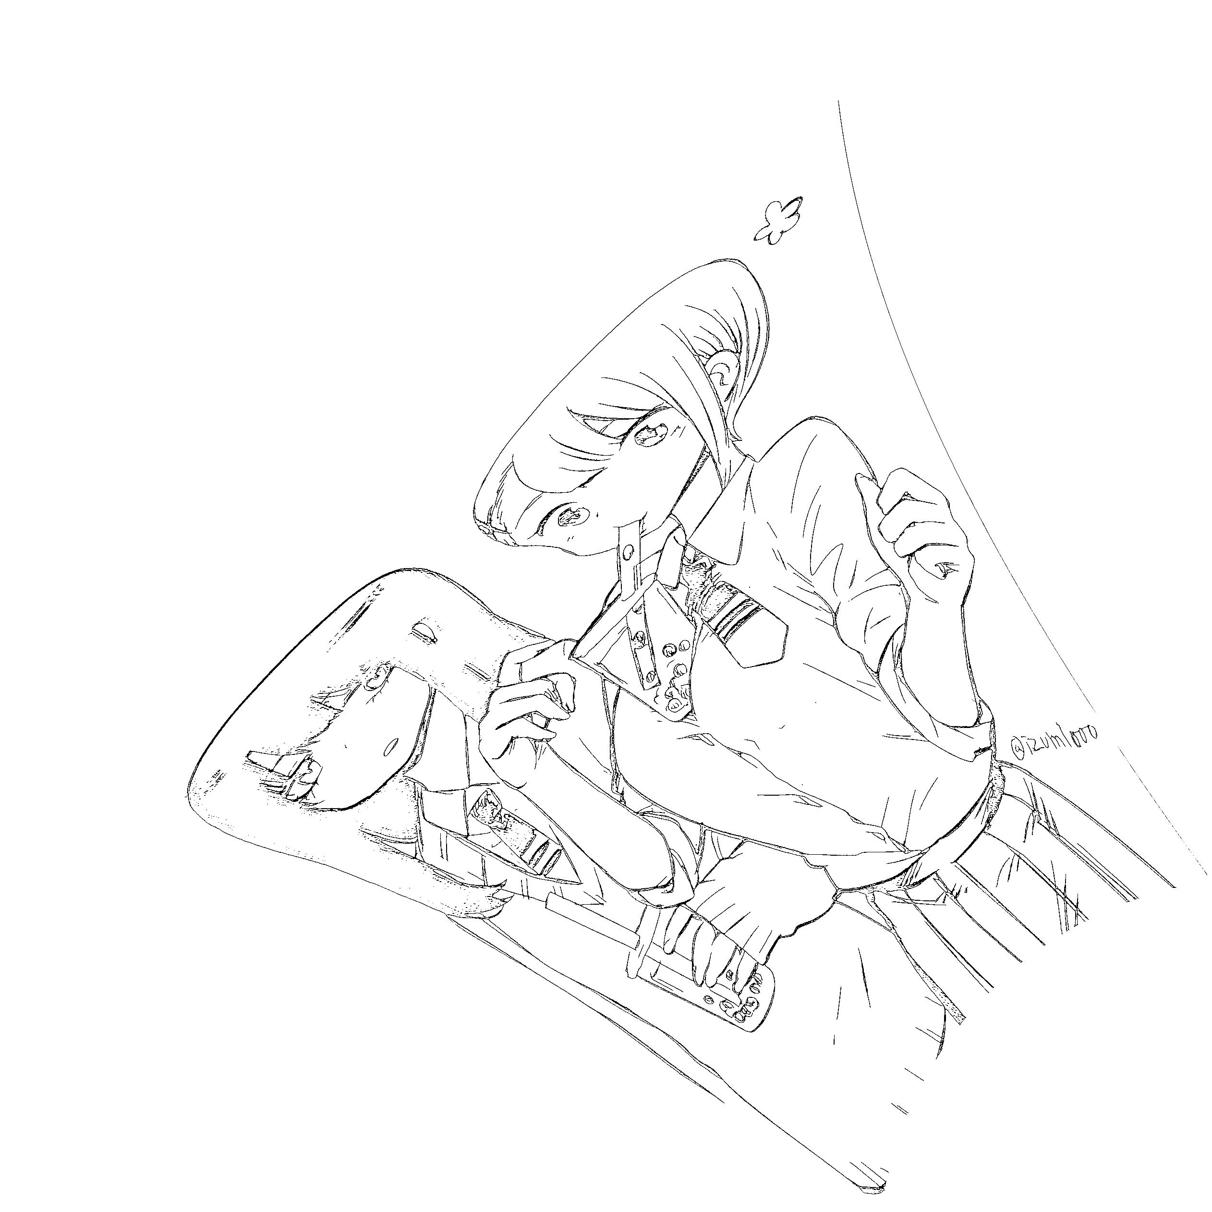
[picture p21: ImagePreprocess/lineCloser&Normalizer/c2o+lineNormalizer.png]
|||

## 碎线移除

太短的线没必要画出来，影响效率，还让画面变得很乱，因此需要去除这些碎线。代码在 shortRemove.py，对LineCloser+LineNormalizer+otsu处理后的图像进行碎线移除，效果如下：

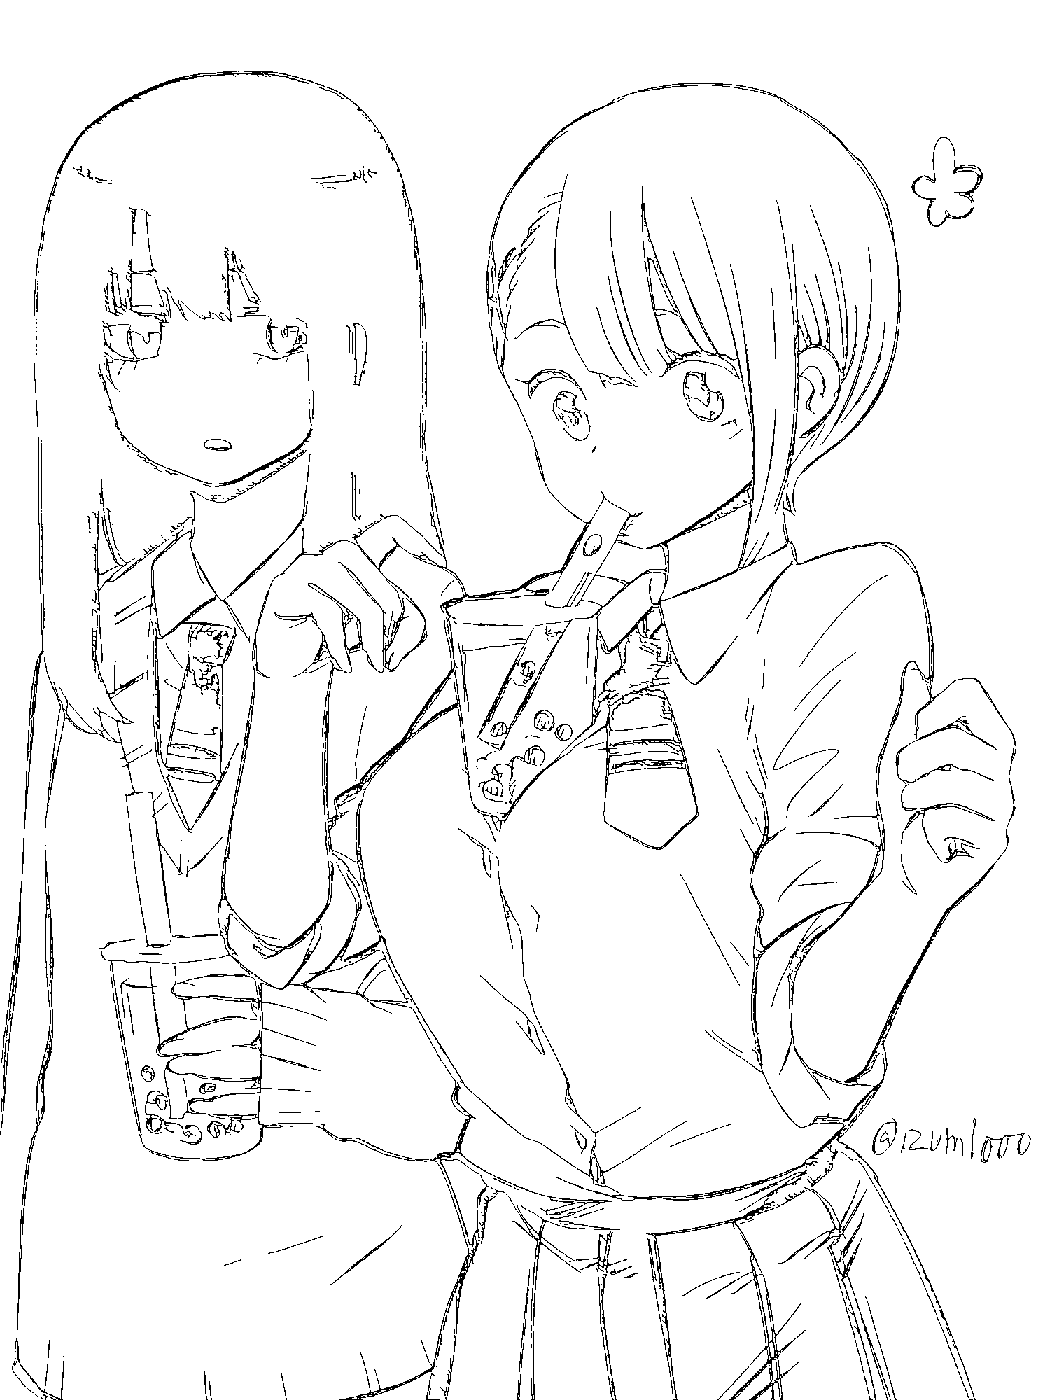
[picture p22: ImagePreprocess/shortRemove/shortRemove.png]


# 处理顺序

素描化 ==> 二值化 ==> LineCloser ==> 碎线移除 ==> c2o ==> LineNormalizer

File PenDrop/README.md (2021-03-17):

# 下笔

我们用一舵机来控制笔的起落。虽然看起来很简单，但我们要考虑一个问题：下笔的轻重。

但因为我不想考虑这个问题，所以我们无视它。

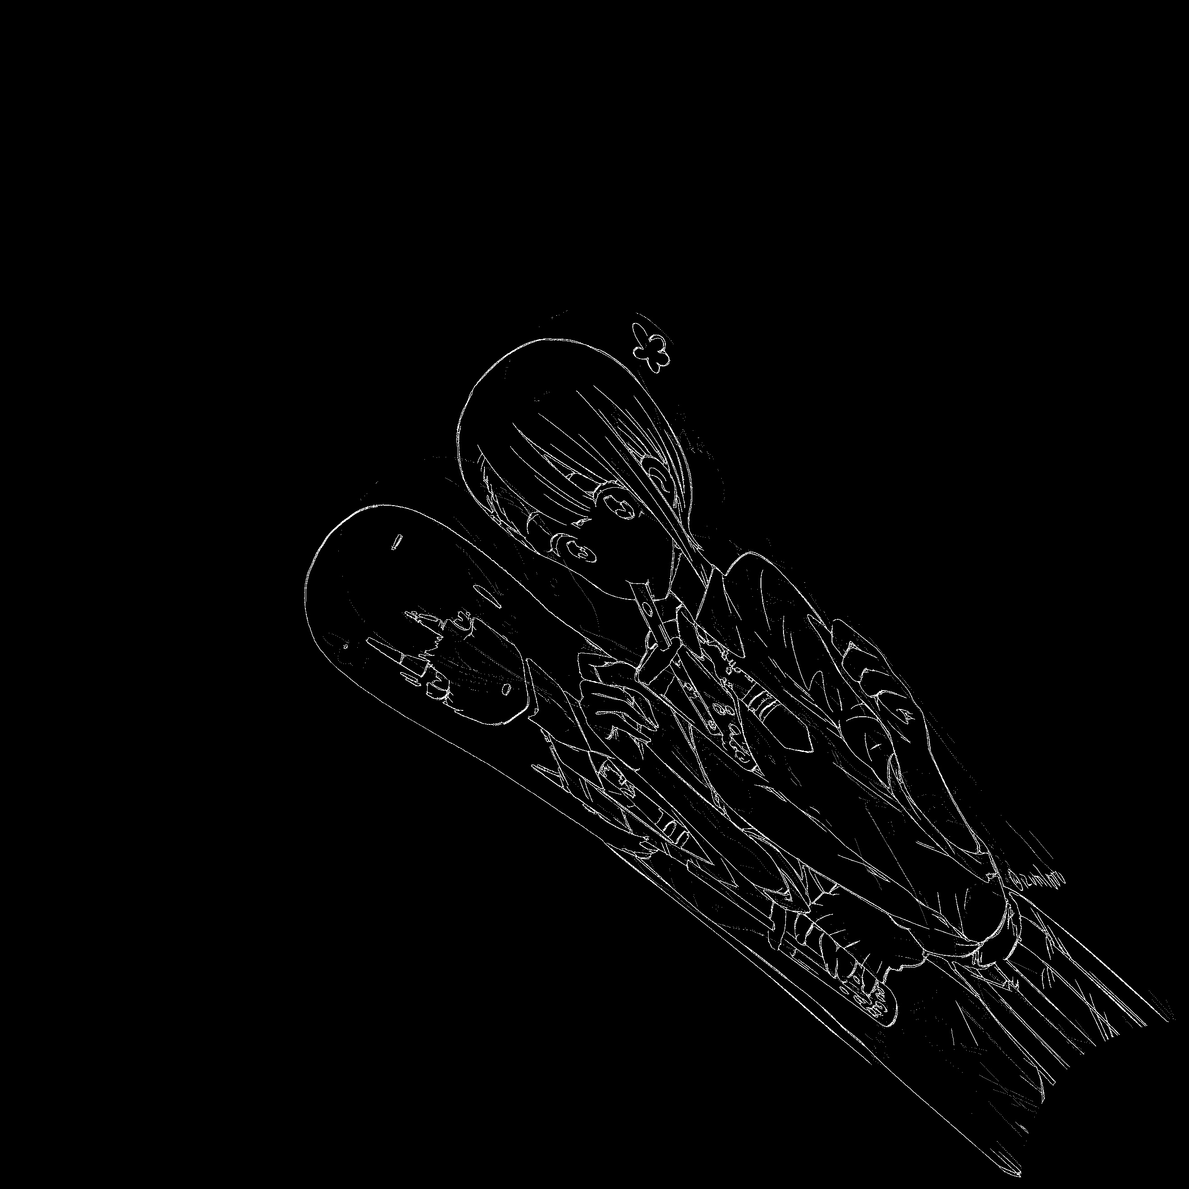
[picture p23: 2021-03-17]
image_draw.jpg

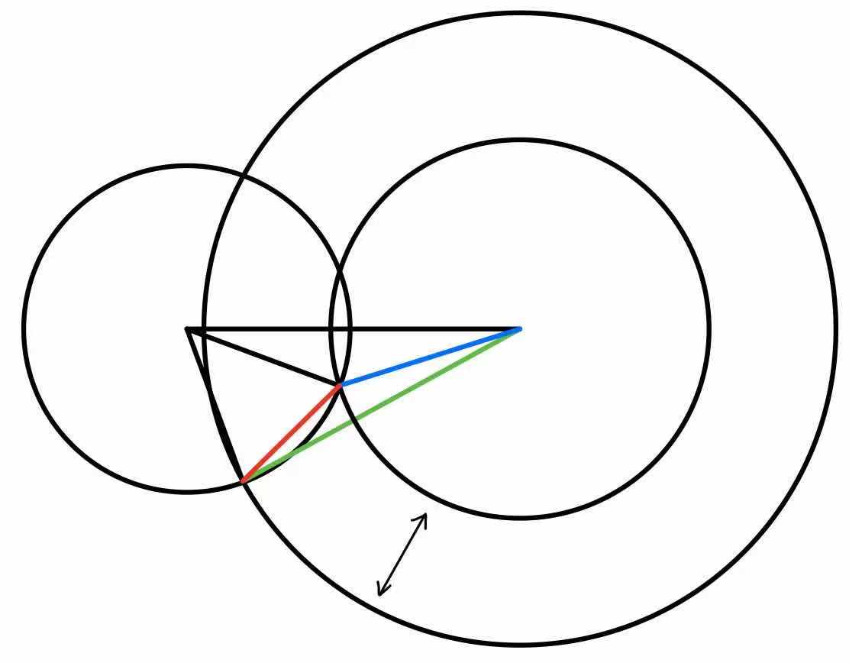
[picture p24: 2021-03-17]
assets/images/最小移动距离.jpg

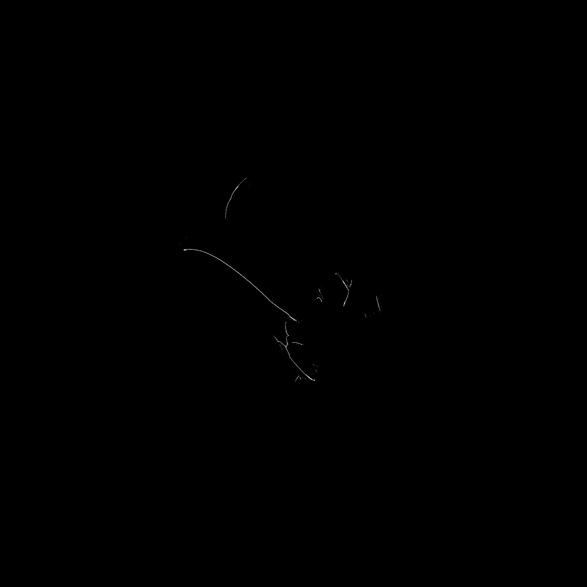
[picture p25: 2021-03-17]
image_draw2.jpg

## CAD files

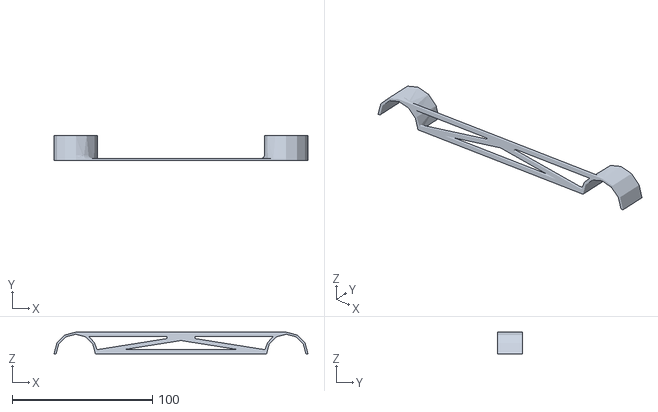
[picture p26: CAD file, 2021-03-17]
3Dprint/motor_holder.stl
181.0 x 18.0 x 15.5

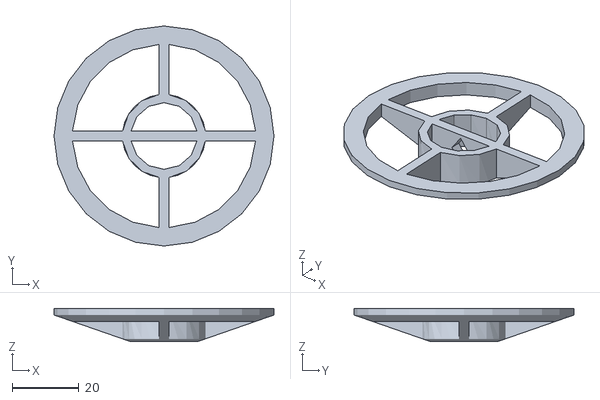
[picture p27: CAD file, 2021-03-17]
3Dprint/pen_ufo.stl
66.0 x 66.0 x 10.0

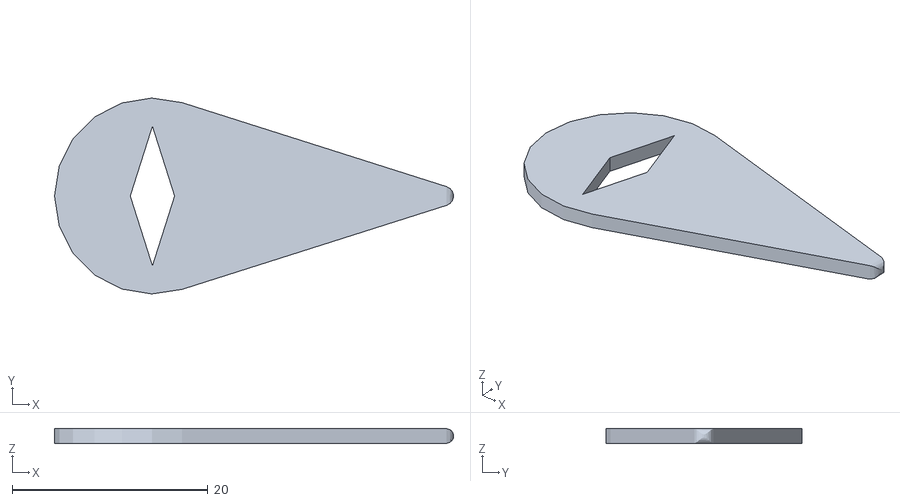
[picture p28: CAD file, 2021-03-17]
3Dprint/temp_pen.stl
40.7 x 20.0 x 1.50

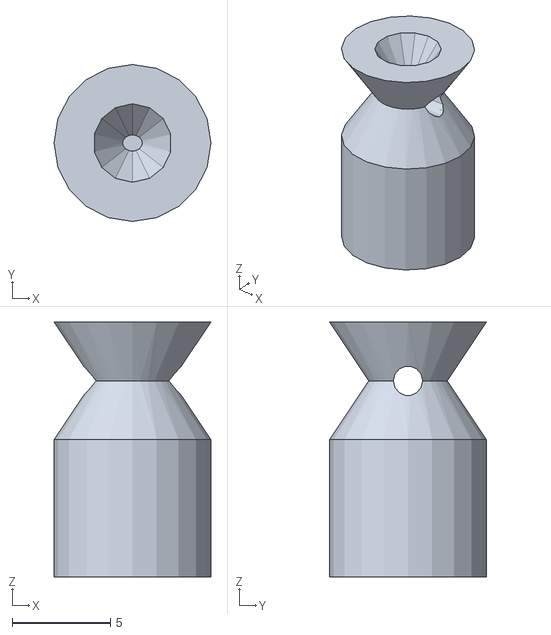
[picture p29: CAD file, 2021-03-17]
3Dprint/axis_shell.stl
8.00 x 8.00 x 13.0

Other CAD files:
3Dprint/axis_shell.prt
3Dprint/motor_holder.prt
3Dprint/temp_pen.prt

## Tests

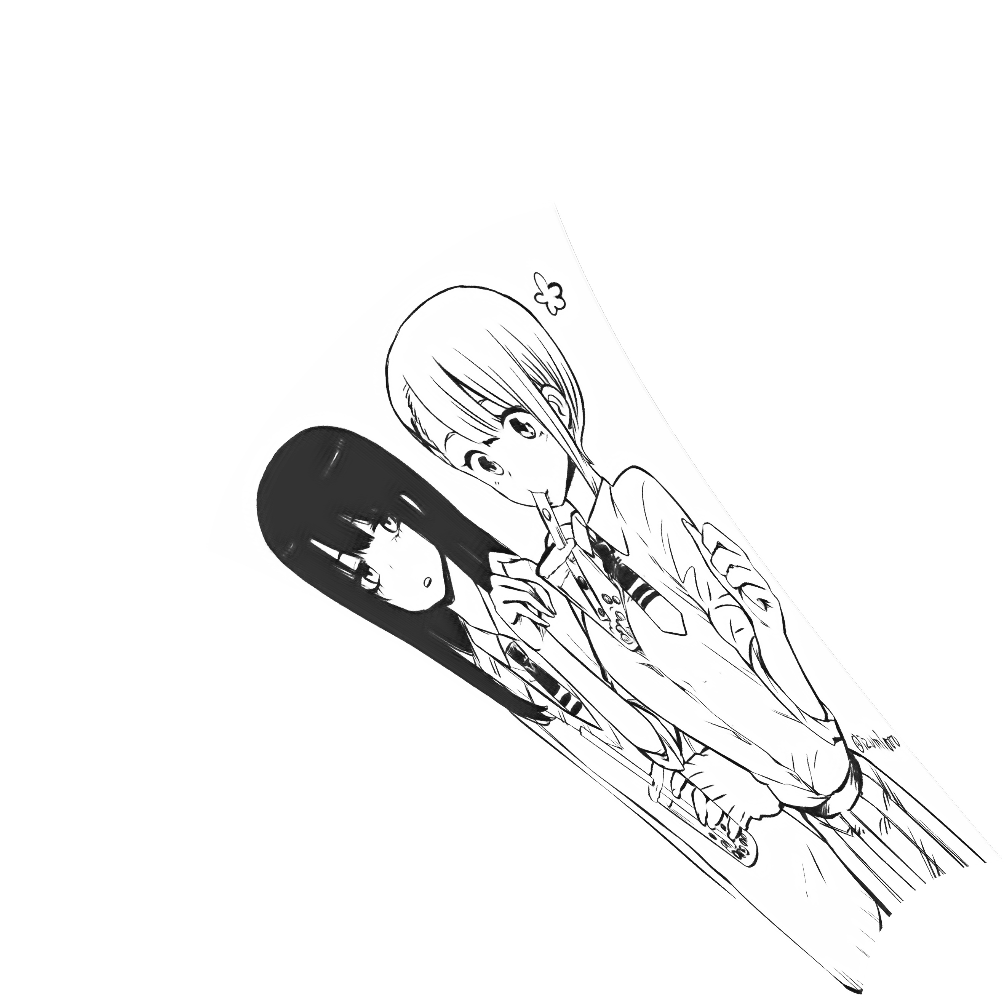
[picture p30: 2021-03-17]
test.jpg

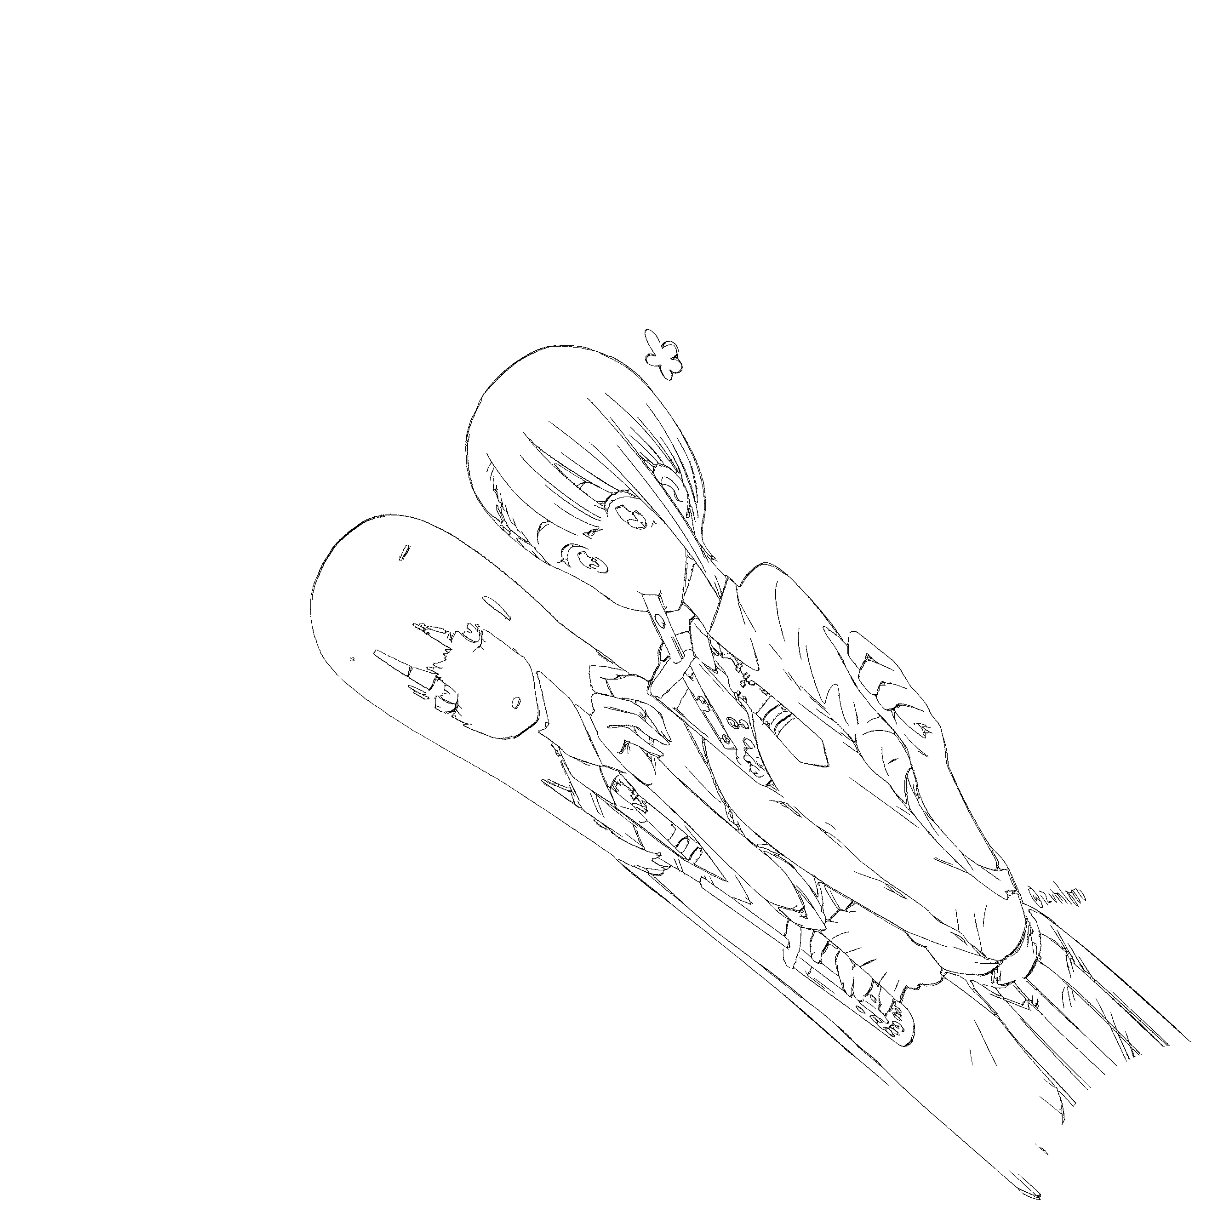
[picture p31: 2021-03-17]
test/final.png

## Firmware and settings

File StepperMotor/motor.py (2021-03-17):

import math
import ctypes
import RPi.GPIO as GPIO

libc = ctypes.CDLL("libc.so.6")
GPIO.setmode(GPIO.BCM)
class Motor_28byj48:
    stride_angle = 5.625 # in degree
    gear_ratios = 63.68395 # or 64
    step_pattern = [
        [1,0,0,0], # pattern 0
        [1,1,0,0],
        [0,1,0,0],
        [0,1,1,0],
        [0,0,1,0],
        [0,0,1,1],
        [0,0,0,1],
        [1,0,0,1]  # pattern 7
    ]
    delay=900 # in us

    def __init__(self, r, step_length, pins):
        self.stride_length = 2*math.pi*r*self.stride_angle/360/self.gear_ratios
        self.step_length = step_length
        self.pins = pins
        self.steps_now = -1
        GPIO.setwarnings(False)
        for i in pins:
            GPIO.setup(i, GPIO.OUT)

        print("A motor class is created. Please initialize it.")

    def initialize(self, init_thread_length):
        self.steps_now = int(init_thread_length / (self.step_length * self.stride_length))
        self.steps_now -= self.steps_now%8
        print("The motor has been initialized.")

    def rotate(self, steps):
        if steps > 0:
            clockwise=-1
        elif steps<0:
            clockwise=1
        else:
            return

        if self.steps_now==-1:
            #if clockwise, then pattern start from 1 to 7 to 0
            #else then pattern start from 7 to 0
            start = int(4-clockwise*3)
            stop = int(4+clockwise*5)
            for i in range(abs(steps)):
                for j in range(start, stop, clockwise):
                    for k in range(4):
                        GPIO.output(self.pins[k], self.step_pattern[j%8][k])
                    libc.usleep(self.delay)
        else:
            for i in range(abs(steps)):
                self.steps_now-=clockwise
                for k in range(4):
                    GPIO.output(self.pins[k], self.step_pattern[self.steps_now%8][k])
                libc.usleep(self.delay)
                
        for k in range(4):
            GPIO.output(self.pins[k], 0)

    def move(self, thread_length):
        steps_next = int(thread_length/(self.step_length*self.stride_length))
        steps = steps_next - self.steps_now
        print("move to", steps_next, "from", self.steps_now)
        self.rotate(steps)
        
def test():
    motor_a = Motor_28byj48(r=3, step_length=1, pins=[4,17,23,24])
    #motor_a.rotate(1)
    motor_a.initialize(100)
    motor_a.move(100.5)
    libc.usleep(400000)
    motor_a.move(100)
    
if __name__ == "__main__":
    test()

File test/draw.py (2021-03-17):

# Woddpecker writing machine
# Author: ToddZhouFeng, aka Todd Zhou
# Date: 2021/01/25

import ctypes
import math
#import threading

import cv2
import numpy as np
import RPi.GPIO as GPIO

libc = ctypes.CDLL("libc.so.6")
GPIO.setmode(GPIO.BCM)
GPIO.setwarnings(False)

# 步进电机驱动
class Motor_28byj48:
    stride_angle = 5.625 # in degree
    gear_ratios = 64 # or 64
    step_pattern = [
        [1,0,0,0], # pattern 0
        [1,1,0,0],
        [0,1,0,0],
        [0,1,1,0],
        [0,0,1,0],
        [0,0,1,1],
        [0,0,0,1],
        [1,0,0,1]  # pattern 7
    ]
    delay=900 # in us

    def __init__(self, r, step_length, pins, direction=1):
        self.stride_length = 2*math.pi*r*self.stride_angle/360/self.gear_ratios
        self.step_length = step_length
        self.pins = pins
        self.steps_now = -1
        self.direction = direction
        GPIO.setwarnings(False)
        for i in pins:
            GPIO.setup(i, GPIO.OUT)

        print("A motor class is created. Please initialize it.")

    def initialize(self, init_thread_length):
        self.steps_now = int(init_thread_length / (self.step_length * self.stride_length))
        self.steps_now -= self.steps_now%8
        print("The motor has been initialized.")

    def rotate(self, steps):
        if steps>0:
            clockwise=-1*self.direction
        elif steps<0:
            clockwise=1*self.direction
        else:
            return

        if self.steps_now==-1:
            #if clockwise, then pattern start from 1 to 7 to 0
            #else then pattern start from 7 to 0
            start = int(4-clockwise*3)
            stop = int(4+clockwise*5)
            for i in range(abs(steps)):
                for j in range(start, stop, clockwise):
                    for k in range(4):
                        GPIO.output(self.pins[k], self.step_pattern[j%8][k])
                    libc.usleep(self.delay)
        else:
            for i in range(abs(steps)):
                self.steps_now-=clockwise
                for k in range(4):
                    GPIO.output(self.pins[k], self.step_pattern[self.steps_now%8][k])
                libc.usleep(self.delay)
                
        for k in range(4):
            GPIO.output(self.pins[k], 0)

    def move(self, thread_length):
        steps_next = int(thread_length/(self.step_length*self.stride_length))
        steps = (steps_next - self.steps_now)
        print("move to", steps_next, "from", self.steps_now)
        self.rotate(steps)

#查找最近点
def search(image, index_now):
    distance=0
    height=image.shape[0]
    width=image.shape[1]
    no_result=4
    while no_result != 0:
        distance+=1
        no_result=4
        k=0
        l=0
        if index_now[1]-distance>=0:
            #print(1, end='')
            for i in range(distance-1,-distance,-1):
                k=index_now[0]+i
                l=index_now[1]-distance
                if k>=0 and l>=0 and k<width and l < height and image[l, k]==1:
                    return [k, l]
            if index_now[0]-distance>=0:
                k-=1
                if k>=0 and l>=0 and k<width and l < height and image[l,k]==1:
                    return [l, k]
        else:
            no_result-=1
        if index_now[0]-distance>=0:
            #print(2, end='')
            for i in range(-distance+1,distance):
                k=index_now[0]-distance
                l=index_now[1]+i
                if k>=0 and l>=0 and k<width and l < height and image[l, k]==1:
                    return [k, l]
            if index_now[1]+distance<height:
                l+=1
                if k>=0 and l>=0 and k<width and l < height and image[l, k]==1:
                    return [k, l]
        else:
            no_result-=1
        if index_now[1]+distance<height:
            #print(3, end='')
            for i in range(-distance+1,distance):
                k=index_now[0]+i
                l=index_now[1]+distance
                if k>=0 and l>=0 and k<width and l < height and image[l, k]==1:
                    return [k, l]
            if index_now[0]+distance<width:
                k+=1
                if k>=0 and l>=0 and k<width and l < height and image[l, k]==1:
                    return [k, l]
        else:
            no_result-=1
        if index_now[0]+distance<width:
            #print(4)
            for i in range(distance-1,-distance,-1):
                k=index_now[0]+distance
                l=index_now[1]+i
                if k>=0 and l>=0 and k<width and l < height and image[l, k]==1:
                    return [k, l]
            if index_now[1]-distance>=0:
                l-=1
                if k>=0 and l>=0 and k<width and l < height and image[l, k]==1:
                    return [k, l]
        else:
            no_result-=1
    return None

#判断是否相邻
def is_next_to(index_a, index_b):
    if abs(index_a[0]-index_b[0])<=1 and \
        abs(index_a[1]-index_b[1])<=1:
        return True
    else:
        return False

#像素转线长
def index2length(index, step_length, oval=1, w=0):
    a_A = index[0]*step_length
    a_B = index[1]*step_length
    if oval==1:
        return [a_A, a_B]
    elif oval>1 and w>0:
        x = (a_A**2-a_B**2)/(2*w*oval**2)+w/2
        y = math.sqrt(a_A**2-(x**2)*(oval**2))
        a = math.sqrt(x**2+y**2)
        b = math.sqrt((w-x)**2+y**2)
        return [a, b]
    else:
        print("c2o error")
        return False

is_drop=0
#下笔
def drop():
    print("下笔")
    global is_drop
    is_drop=1
    
#抬笔
def lift():
    print("    抬笔")
    global is_drop
    is_drop=0

def main():
    image = 1-cv2.imread("final.png", cv2.IMREAD_GRAYSCALE)/255
    image = image.astype(np.uint8)
    motor_a = Motor_28byj48(r=2.1, step_length=1, pins=[4,18,23,24], direction=1)
    motor_b = Motor_28byj48(r=2.1, step_length=1, pins=[5,6,13,19], direction=1)
    motor_a.initialize(68)
    motor_b.initialize(158)
    global is_drop
    index_now=[0,0]
    while True:
        index_next=search(image, index_now)
        print(index_next)
        if index_next == None:
            break
        if not is_next_to(index_next, index_now) and is_drop:
            lift()
        thread_length_a, thread_length_b = index2length(index_next, 0.0046*25)
        print(thread_length_a, thread_length_b)
        motor_a.move(thread_length_a)
        motor_b.move(thread_length_b)
        if not is_drop:
            drop()
        image[index_now[1], index_now[0]] = 0
#         try:
#             for i in (-1, 0, 1):
#                 for j in (-1, 0, 1):
#                     image[index_now[1]+i, index_now[0]+j] = 0
#         except:
#             pass
        index_now[0]=index_next[0]
        index_now[1]=index_next[1]
        

main()
